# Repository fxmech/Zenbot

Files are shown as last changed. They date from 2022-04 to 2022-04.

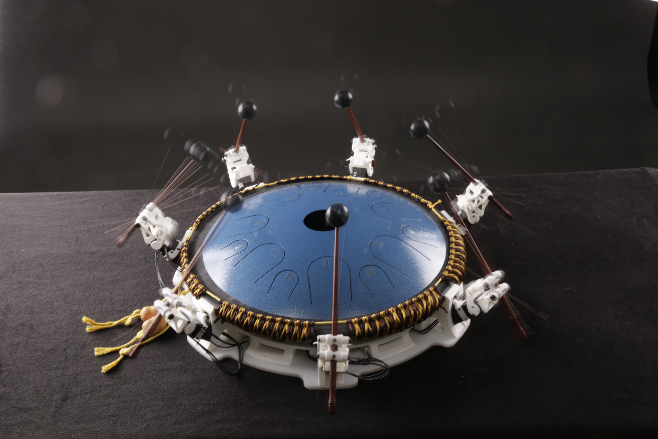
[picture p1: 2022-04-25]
_MG_4377.JPG

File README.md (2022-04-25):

# Zenbot
Zenbot is a project featured in MAKE Magazine that consists of seven robots playing 14 notes on a tongue drum
This repository will hold CAD files as well as arduino code.
Instructional videos to support the MAKE Magazine article can be found at:
https://www.youtube.com/playlist?list=PL2LZ_0VrozM2b-Bjvy_ZAQbU2o-aZzOwE
Article is available through https://makezine.com/

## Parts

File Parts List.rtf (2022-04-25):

Parts list:
ROBOTIS (https://www.robotis.us/ )
14 pcs Dynamixel xl330-m288-t servo
1 pk Robot cable X3P 240mm
2 pk Robot cable X3P 100mm
1 pk Robot cable X3P 180mm (Convertible)
1pc U2D2 (servo programmer)
1pc U2D2 Hub Board adapter
1pc OpenCM 485 Expansion Board
1pc OpenCM9.04-C microcontroller

Amazon
1pc AC to DC power adapter: AC Input: 100-240V 50/60Hz 1.0A, DC Output: 6V 3A
Amazon.com: Belker 36W Universal 3V 4.5V 5V 6V 7.5V 9V 12V AC DC Adapter Power Supply for LCD LED Light Strip Router HUB Speaker Smart Phone TV Box 1A 1.5A 2A 2.5A 3A 3000mA Amp Max. : Electronics (https://www.amazon.com/gp/product/B07N18XN84/ref=ppx_yo_dt_b_asin_title_o00_s00?ie=UTF8&psc=1)

1pk Generic 40 Pin Breakaway Headers 0.1" Male Equal Length Long Centered 6.25mm on Both Sides 15mm in Total(pack of 10)

5 Pcs 10k Linear Potentiometer, 10K Ohm 3 Pin Linear Taper Adjustable Rotary Potentiometer
https://www.amazon.com/Linear-Potentiometer-Adjustable-Connector-Resistance/dp/B09MS1T32Z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 (https://www.amazon.com/Linear-Potentiometer-Adjustable-Connector-Resistance/dp/B09MS1T32Z)

eBay
14inch Tongue Drum Handpan Pan Drum 14 Notes Hand Pan Drum Percussion Instrument
https://www.ebay.com/itm/233595745739

2pcs Wood Drum Sticks Steel Tongue Drum Mallets (4 come per order. You will need 7pcs total)
https://www.ebay.com/itm/184510420465

McMaster-Carr
10ft 3286T11 Buna-N O-Ring Cord, Oil-Resistant, 0.07" Actual Width, White
1 box 97763A143 Button Head 6-32 Thread Size, 1/2" Long screws (28 screws needed)
1 box 93791A453 Flat Head 6-32 Thread Size, 3/8" Long screws (21 screws needed)
97763A232 Button Head 10-32 Thread Size, 1/2" Long screws (28 screws needed)
92610A108 Socket Head 4-40 Thread Size, 1/4" Long screws (14 screws needed)
8505K757 Cast Acrylic Sheet, 24" x 24" x 1/4" Color: White

Optional:
4pks https://www.musiciansfriend.com/accessories/timber-drum-company-soft-rubber-mallets

Tools Used:
Computer and USB Micro Cable for programming Dynamixel servos (free online software needed)
3D printer with Tough PLA or other similar filament.
Hot Glue Gun
Drills, Taps, and reamers and countersink for finishing holes
Basic tools for cleaning 3d printed parts (sand paper, files, hobby knives, etc.)
Basic electronic tools (Iron, multimeter, wire, heat shrink, etc.)
Access to laser cutter or laser cutting service to cut base out of acrylic. Base can also be made from wood or 3d printed in smaller sections.

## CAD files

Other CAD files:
Zenbot.f3d

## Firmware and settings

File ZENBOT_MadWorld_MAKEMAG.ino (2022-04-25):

//ZENBOT 14-Servo Tongue Drum Player
//David Covarrubias
//fxmech@cammotion.net

#include <Dynamixel2Arduino.h>
#if defined(ARDUINO_AVR_UNO) || defined(ARDUINO_AVR_MEGA2560) // When using DynamixelShield
#include <SoftwareSerial.h>
SoftwareSerial soft_serial(7, 8); // DYNAMIXELShield UART RX/TX
#define DXL_SERIAL   Serial
#define DEBUG_SERIAL soft_serial
const uint8_t DXL_DIR_PIN = 2; // DYNAMIXEL Shield DIR PIN
#elif defined(ARDUINO_SAM_DUE) // When using DynamixelShield
#define DXL_SERIAL   Serial
#define DEBUG_SERIAL SerialUSB
const uint8_t DXL_DIR_PIN = 2; // DYNAMIXEL Shield DIR PIN
#elif defined(ARDUINO_SAM_ZERO) // When using DynamixelShield
#define DXL_SERIAL   Serial1
#define DEBUG_SERIAL SerialUSB
const uint8_t DXL_DIR_PIN = 2; // DYNAMIXEL Shield DIR PIN
#elif defined(ARDUINO_OpenCM904) // When using official ROBOTIS board with DXL circuit.
#define DXL_SERIAL   Serial3 //OpenCM9.04 EXP Board's DXL port Serial. (Serial1 for the DXL port on the OpenCM 9.04 board)
#define DEBUG_SERIAL Serial
const uint8_t DXL_DIR_PIN = 22; //OpenCM9.04 EXP Board's DIR PIN. (28 for the DXL port on the OpenCM 9.04 board)
#elif defined(ARDUINO_OpenCR) // When using official ROBOTIS board with DXL circuit.
#define DXL_SERIAL   Serial3
#define DEBUG_SERIAL Serial
const uint8_t DXL_DIR_PIN = 84; // OpenCR Board's DIR PIN.
#else // Other boards when using DynamixelShield
#define DXL_SERIAL   Serial1
#define DEBUG_SERIAL Serial
const uint8_t DXL_DIR_PIN = 2; // DYNAMIXEL Shield DIR PIN
#endif
const float DXL_PROTOCOL_VERSION = 2.0;

const int buttonPin = 16; //built in button on OpenCM Expansion Board
int buttonState = 0;

int malletRotateLowNote[8] = {0, 1975, 1975, 1975, 1975, 1975, 1975, 1997};//low octave
int malletRotateHighNote[8] = {0, 1776, 1776, 1795, 1730, 1753, 1800, 1731};//high octave
int malletUp = 1625;
int malletDown = 2121;

int reorder[8] = {0, 1, 3, 2, 7, 5, 4, 6}; 

int a;
int startFrame = 0;
int endFrame = 15;
int time2Move = 150; //millis that mallet spends dropping before it reverses direction

// 0= no note  1=low note loud  2= high note loud
int notesC[160] = {0, 0, 0, 0, 0, 0, 0, 0, 0, 0, 1, 0, 0, 0, 1, 0, 1, 0, 0, 0, 1, 0, 0, 0, 0, 0, 0, 0, 0, 0, 0, 0,    0, 0, 0, 0, 0, 0, 0, 0, 0, 0, 1, 0, 0, 0, 1, 0, 1, 0, 0, 0, 1, 0, 0, 0, 0, 0, 0, 0, 0, 0, 0, 0,   0, 0, 0, 0, 0, 0, 0, 0, 0, 0, 0, 0, 0, 0, 0, 0, 0, 0, 0, 0, 0, 0, 0, 0, 0, 0, 0, 0, 0, 0, 0, 0,    0, 0, 0, 0, 0, 0, 0, 0, 0, 0, 0, 0, 0, 0, 0, 0, 0, 0, 0, 0, 0, 0, 0, 0, 0, 0, 0, 0, 0, 0, 0, 0,    0, 0, 0, 0, 0, 0, 1, 0, 0, 0, 0, 0, 0, 0, 0, 0, 0, 0, 0, 0, 0, 0, 1, 0, 0, 0, 0, 0, 0, 0, 0, 0};
int notesD[160] = {1, 0, 1, 1, 0, 0, 2, 2, 0, 0, 0, 0, 0, 0, 0, 0, 0, 0, 0, 0, 0, 0, 0, 0, 0, 0, 1, 0, 0, 0, 1, 1,    0, 0, 1, 1, 0, 0, 2, 2, 0, 0, 0, 0, 0, 0, 0, 0, 0, 0, 0, 0, 0, 0, 0, 0, 1, 0, 0, 0, 0, 0, 0, 1,   0, 0, 1, 1, 1, 0, 0, 0, 0, 0, 1, 0, 0, 1, 1, 0, 1, 0, 0, 1, 1, 0, 0, 0, 0, 0, 1, 0, 0, 0, 1, 0,    2, 0, 1, 2, 1, 0, 0, 0, 0, 0, 1, 0, 0, 1, 1, 0, 1, 0, 0, 1, 1, 0, 0, 0, 1, 0, 0, 0, 0, 0, 0, 0,    1, 0, 0, 0, 1, 1, 0, 0, 0, 0, 1, 0, 0, 0, 1, 0, 1, 0, 0, 0, 1, 1, 0, 0, 0, 0, 1, 0, 0, 0, 1, 0};
int notesE[160] = {0, 0, 0, 0, 0, 0, 0, 0, 0, 0, 0, 0, 0, 0, 0, 0, 0, 0, 1, 0, 0, 1, 1, 0, 0, 0, 0, 0, 0, 0, 1, 0,    0, 0, 0, 0, 0, 0, 0, 0, 0, 0, 0, 0, 0, 0, 0, 0, 0, 0, 1, 0, 0, 1, 1, 0, 0, 0, 0, 0, 0, 0, 1, 0,   0, 0, 0, 0, 0, 0, 0, 0, 0, 0, 0, 0, 0, 0, 0, 0, 0, 0, 0, 0, 0, 0, 0, 0, 0, 0, 0, 0, 0, 0, 0, 0,    0, 0, 0, 0, 0, 0, 0, 0, 0, 0, 0, 0, 0, 0, 0, 0, 0, 0, 0, 0, 0, 0, 0, 0, 0, 0, 0, 0, 0, 0, 0, 0,    0, 0, 1, 1, 0, 0, 0, 0, 0, 0, 0, 0, 0, 0, 0, 0, 0, 0, 1, 1, 0, 0, 0, 0, 0, 0, 0, 0, 0, 0, 0, 0};
int notesF[160] = {0, 0, 1, 0, 2, 2, 1, 0, 1, 0, 0, 0, 1, 2, 0, 0, 0, 0, 0, 0, 0, 0, 0, 0, 0, 0, 0, 0, 0, 2, 0, 0,    0, 0, 1, 0, 2, 2, 1, 0, 1, 0, 0, 0, 1, 2, 0, 0, 0, 0, 0, 0, 0, 0, 0, 0, 0, 0, 0, 0, 0, 2, 0, 0,   0, 0, 1, 0, 2, 2, 1, 0, 0, 0, 0, 0, 0, 0, 0, 0, 0, 0, 1, 0, 2, 2, 2, 0, 0, 0, 0, 0, 0, 0, 0, 0,    0, 0, 0, 0, 2, 2, 1, 0, 0, 0, 0, 0, 0, 0, 0, 0, 0, 0, 1, 0, 2, 2, 2, 0, 0, 0, 0, 0, 0, 0, 0, 0,    2, 2, 1, 0, 2, 0, 1, 0, 0, 0, 0, 0, 0, 0, 0, 2, 0, 2, 1, 0, 2, 0, 1, 0, 0, 0, 0, 0, 0, 0, 0, 0};
int notesG[160] = {0, 0, 0, 0, 0, 0, 0, 0, 0, 0, 0, 0, 0, 0, 0, 0, 2, 2, 1, 2, 0, 0, 1, 0, 2, 2, 0, 2, 1, 0, 0, 0,    0, 0, 0, 0, 0, 0, 0, 0, 0, 0, 0, 0, 0, 0, 0, 0, 2, 2, 1, 2, 0, 0, 1, 0, 2, 2, 0, 2, 0, 0, 0, 0,   0, 0, 0, 0, 0, 0, 0, 0, 1, 2, 0, 2, 1, 0, 2, 2, 0, 0, 0, 0, 0, 0, 0, 0, 1, 2, 2, 2, 1, 0, 2, 2,    0, 0, 0, 0, 0, 0, 0, 0, 1, 2, 0, 2, 1, 0, 2, 2, 0, 0, 0, 0, 0, 0, 0, 0, 1, 2, 2, 2, 0, 0, 2, 2,    0, 0, 0, 0, 0, 0, 0, 0, 1, 0, 0, 0, 1, 0, 0, 0, 0, 0, 0, 0, 0, 0, 0, 2, 1, 0, 0, 0, 1, 0, 0, 0};
int notesA[160] = {0, 0, 1, 0, 0, 0, 1, 0, 2, 2, 1, 2, 0, 0, 1, 0, 0, 0, 0, 0, 0, 0, 0, 0, 0, 0, 0, 0, 0, 0, 0, 0,    0, 0, 1, 0, 0, 0, 1, 0, 2, 2, 1, 2, 0, 0, 1, 0, 0, 0, 0, 0, 0, 0, 0, 0, 0, 0, 0, 0, 0, 0, 0, 0,   0, 0, 1, 0, 0, 0, 2, 2, 0, 0, 0, 0, 0, 0, 0, 0, 0, 0, 1, 0, 0, 0, 2, 2, 0, 0, 1, 0, 0, 0, 1, 0,    0, 0, 1, 0, 0, 0, 2, 2, 0, 0, 0, 0, 0, 0, 0, 0, 0, 0, 1, 0, 0, 0, 2, 2, 0, 0, 0, 0, 0, 0, 0, 0,    2, 2, 1, 0, 0, 0, 1, 0, 0, 0, 0, 0, 0, 0, 0, 0, 0, 2, 1, 0, 0, 0, 1, 0, 0, 0, 0, 0, 0, 0, 0, 0};
int notesB[160] = {0, 0, 0, 0, 0, 0, 0, 0, 0, 0, 0, 0, 0, 0, 0, 0, 0, 0, 0, 0, 0, 0, 0, 0, 0, 0, 1, 0, 0, 0, 1, 0,    0, 0, 0, 0, 0, 0, 0, 0, 0, 0, 0, 0, 0, 0, 0, 0, 0, 0, 0, 0, 0, 0, 0, 0, 1, 0, 0, 0, 0, 0, 0, 0,   0, 0, 0, 0, 0, 0, 0, 0, 2, 0, 1, 0, 2, 2, 1, 0, 0, 0, 0, 0, 0, 0, 0, 0, 2, 0, 0, 0, 2, 2, 0, 0,    0, 0, 0, 0, 0, 0, 0, 0, 2, 0, 1, 0, 2, 2, 1, 0, 0, 0, 0, 0, 0, 0, 0, 0, 2, 0, 0, 0, 2, 2, 0, 0,    0, 0, 0, 0, 0, 0, 0, 1, 0, 0, 1, 0, 0, 0, 1, 0, 0, 0, 0, 0, 0, 0, 0, 1, 0, 0, 1, 0, 0, 0, 1, 0};

Dynamixel2Arduino dxl(DXL_SERIAL, DXL_DIR_PIN);

//This namespace is required to use Control table item names
using namespace ControlTableItem;

void setup() {
  pinMode(buttonPin, INPUT); //Start Button Pin

  // Use UART port of DYNAMIXEL Shield to debug.
  //DEBUG_SERIAL.begin(115200);
  //while(!DEBUG_SERIAL);
  dxl.begin(1000000);
  // Set Port Protocol Version. This has to match with DYNAMIXEL protocol version.
  dxl.setPortProtocolVersion(DXL_PROTOCOL_VERSION);
  // Get DYNAMIXEL information
  for (int i = 1; i < 8; i++) {
    dxl.ping(i);
    dxl.ping(i + 10);
    delay(100);
  }

  // Turn off torque when configuring items in EEPROM area
  for (int i = 1; i < 8; i++) {
    dxl.torqueOff(i);
    dxl.setOperatingMode(i, OP_POSITION);
    dxl.torqueOn(i);
    dxl.torqueOff(i + 10);
    dxl.setOperatingMode(i + 10, OP_POSITION);
    dxl.torqueOn(i + 10);
    delay(100);
  }

  // Limit the maximum velocity in Position Control Mode. Use 0 for Max speed
  for (int i = 1; i < 8; i++) {
    dxl.writeControlTableItem(PROFILE_VELOCITY, i, 0);
    dxl.writeControlTableItem(PROFILE_VELOCITY, i + 10, 0);
    dxl.writeControlTableItem(PROFILE_ACCELERATION, i, 0);
    dxl.writeControlTableItem(PROFILE_ACCELERATION, i + 10, 0);
    dxl.setGoalPosition(i, 2024);
    dxl.setGoalPosition(i + 10, 1750);
    delay(100);
  }
  delay(500);
  startAnimation();
}
void playnotesA(int del) {
  startFrame = 0;
  endFrame = 31;

  for (int i = startFrame; i < endFrame + 1; i++) {
    // STRIKE NOTE
    if (notesC[i] == 1 || notesC[i] == 2)  dxl.setGoalPosition(11, malletDown);
    if (notesD[i] == 1 || notesD[i] == 2)  dxl.setGoalPosition(12, malletDown);
    if (notesE[i] == 1 || notesE[i] == 2)  dxl.setGoalPosition(13, malletDown);
    if (notesF[i] == 1 || notesF[i] == 2)  dxl.setGoalPosition(14, malletDown);
    if (notesG[i] == 1 || notesG[i] == 2)  dxl.setGoalPosition(15, malletDown);
    if (notesA[i] == 1 || notesA[i] == 2)  dxl.setGoalPosition(16, malletDown);
    if (notesB[i] == 1 || notesB[i] == 2)  dxl.setGoalPosition(17, malletDown);
    delay(time2Move);

    //PREP FOR NEXT NOTE
    if (i + 1 >= endFrame + 1) a = startFrame; else a = i + 1;
    if (notesC[a] == 1)dxl.setGoalPosition(1, malletRotateLowNote[1]); else dxl.setGoalPosition(1, malletRotateHighNote[1]);
    if (notesD[a] == 1)dxl.setGoalPosition(2, malletRotateLowNote[2]); else dxl.setGoalPosition(2, malletRotateHighNote[2]);
    if (notesE[a] == 1)dxl.setGoalPosition(3, malletRotateLowNote[3]); else dxl.setGoalPosition(3, malletRotateHighNote[3]);
    if (notesF[a] == 1)dxl.setGoalPosition(4, malletRotateLowNote[4]); else dxl.setGoalPosition(4, malletRotateHighNote[4]);
    if (notesG[a] == 1)dxl.setGoalPosition(5, malletRotateLowNote[5]); else dxl.setGoalPosition(5, malletRotateHighNote[5]);
    if (notesA[a] == 1)dxl.setGoalPosition(6, malletRotateLowNote[6]); else dxl.setGoalPosition(6, malletRotateHighNote[6]);
    if (notesB[a] < 3)dxl.setGoalPosition(7, malletRotateLowNote[7]); else dxl.setGoalPosition(7, malletRotateHighNote[7]);
    for (int i = 11; i < 18; i++) {
      dxl.setGoalPosition(i, malletUp);
    }
    delay(del);
  }
}

void playnotesB(int del) {
  startFrame = 32;
  endFrame = 63;

  for (int i = startFrame; i < endFrame + 1; i++) {
    // STRIKE NOTE
    if (notesC[i] == 1 || notesC[i] == 2)  dxl.setGoalPosition(11, malletDown);
    if (notesD[i] == 1 || notesD[i] == 2)  dxl.setGoalPosition(12, malletDown);
    if (notesE[i] == 1 || notesE[i] == 2)  dxl.setGoalPosition(13, malletDown);
    if (notesF[i] == 1 || notesF[i] == 2)  dxl.setGoalPosition(14, malletDown);
    if (notesG[i] == 1 || notesG[i] == 2)  dxl.setGoalPosition(15, malletDown);
    if (notesA[i] == 1 || notesA[i] == 2)  dxl.setGoalPosition(16, malletDown);
    if (notesB[i] == 1 || notesB[i] == 2)  dxl.setGoalPosition(17, malletDown);
    delay(time2Move);

    //PREP FOR NEXT NOTE
    if (i + 1 >= endFrame + 1) a = startFrame; else a = i + 1;
    if (notesC[a] == 1)dxl.setGoalPosition(1, malletRotateLowNote[1]); else dxl.setGoalPosition(1, malletRotateHighNote[1]);
    if (notesD[a] == 1)dxl.setGoalPosition(2, malletRotateLowNote[2]); else dxl.setGoalPosition(2, malletRotateHighNote[2]);
    if (notesE[a] == 1)dxl.setGoalPosition(3, malletRotateLowNote[3]); else dxl.setGoalPosition(3, malletRotateHighNote[3]);
    if (notesF[a] == 1)dxl.setGoalPosition(4, malletRotateLowNote[4]); else dxl.setGoalPosition(4, malletRotateHighNote[4]);
    if (notesG[a] == 1)dxl.setGoalPosition(5, malletRotateLowNote[5]); else dxl.setGoalPosition(5, malletRotateHighNote[5]);
    if (notesA[a] == 1)dxl.setGoalPosition(6, malletRotateLowNote[6]); else dxl.setGoalPosition(6, malletRotateHighNote[6]);
    if (notesB[a] == 1)dxl.setGoalPosition(7, malletRotateLowNote[7]); else dxl.setGoalPosition(7, malletRotateHighNote[7]);
    for (int i = 11; i < 18; i++) {
      dxl.setGoalPosition(i, malletUp);
    }
    delay(del);
  }
}

void playnotesC(int del) {
  startFrame = 64;
  endFrame = 160;

  for (int i = startFrame; i < endFrame + 1; i++) {
    // STRIKE NOTE
    if (notesC[i] == 1 || notesC[i] == 2)  dxl.setGoalPosition(11, malletDown);
    if (notesD[i] == 1 || notesD[i] == 2)  dxl.setGoalPosition(12, malletDown);
    if (notesE[i] == 1 || notesE[i] == 2)  dxl.setGoalPosition(13, malletDown);
    if (notesF[i] == 1 || notesF[i] == 2)  dxl.setGoalPosition(14, malletDown);
    if (notesG[i] == 1 || notesG[i] == 2)  dxl.setGoalPosition(15, malletDown);
    if (notesA[i] == 1 || notesA[i] == 2)  dxl.setGoalPosition(16, malletDown);
    if (notesB[i] == 1 || notesB[i] == 2)  dxl.setGoalPosition(17, malletDown);
    delay(time2Move);

    //PREP FOR NEXT NOTE
    if (i + 1 >= endFrame + 1) a = startFrame; else a = i + 1;
    if (notesC[a] == 1)dxl.setGoalPosition(1, malletRotateLowNote[1]); else dxl.setGoalPosition(1, malletRotateHighNote[1]);
    if (notesD[a] == 1)dxl.setGoalPosition(2, malletRotateLowNote[2]); else dxl.setGoalPosition(2, malletRotateHighNote[2]);
    if (notesE[a] == 1)dxl.setGoalPosition(3, malletRotateLowNote[3]); else dxl.setGoalPosition(3, malletRotateHighNote[3]);
    if (notesF[a] == 1)dxl.setGoalPosition(4, malletRotateLowNote[4]); else dxl.setGoalPosition(4, malletRotateHighNote[4]);
    if (notesG[a] == 1)dxl.setGoalPosition(5, malletRotateLowNote[5]); else dxl.setGoalPosition(5, malletRotateHighNote[5]);
    if (notesA[a] == 1)dxl.setGoalPosition(6, malletRotateLowNote[6]); else dxl.setGoalPosition(6, malletRotateHighNote[6]);
    if (notesB[a] == 1)dxl.setGoalPosition(7, malletRotateLowNote[7]); else dxl.setGoalPosition(7, malletRotateHighNote[7]);
    for (int i = 11; i < 18; i++) {
      dxl.setGoalPosition(i, malletUp);
    }
    delay(del);
  }
}
void lowerAllMallets() { //Slowly lowers all mallets to surface of drum
  for (int i = 1; i < 8; i++) {
    dxl.writeControlTableItem(PROFILE_VELOCITY, i + 10, 30);
    dxl.setGoalPosition(i + 10, malletDown);
    delay(10);
  }
  delay(1000);

  for (int i = 1; i < 8; i++) {
    dxl.writeControlTableItem(PROFILE_VELOCITY, i + 10, 0);
    delay(10);
  }
}
void prepFirstNotes() {
  for (int i = 11; i < 18; i++) { //Mallets UP
    dxl.setGoalPosition(i, malletUp);
    delay(100);
  }
  //PREP FOR FIRST NOTE
  a = 0;
  if (notesC[a] == 1)dxl.setGoalPosition(1, malletRotateLowNote[1]); else dxl.setGoalPosition(1, malletRotateHighNote[1]);
  if (notesD[a] == 1)dxl.setGoalPosition(2, malletRotateLowNote[2]); else dxl.setGoalPosition(2, malletRotateHighNote[2]);
  if (notesE[a] == 1)dxl.setGoalPosition(3, malletRotateLowNote[3]); else dxl.setGoalPosition(3, malletRotateHighNote[3]);
  if (notesF[a] == 1)dxl.setGoalPosition(4, malletRotateLowNote[4]); else dxl.setGoalPosition(4, malletRotateHighNote[4]);
  if (notesG[a] == 1)dxl.setGoalPosition(5, malletRotateLowNote[5]); else dxl.setGoalPosition(5, malletRotateHighNote[5]);
  if (notesA[a] == 1)dxl.setGoalPosition(6, malletRotateLowNote[6]); else dxl.setGoalPosition(6, malletRotateHighNote[6]);
  if (notesB[a] == 1)dxl.setGoalPosition(7, malletRotateLowNote[7]); else dxl.setGoalPosition(7, malletRotateHighNote[7]);
  delay(500);
}

void torqueAllOn() { //turns all servos on
  for (int i = 1; i < 8; i++) {
    dxl.torqueOn(i);
    dxl.torqueOn(i + 10);
    delay(100);
  }
  delay(500);
}

void torqueAllOff() { //turns all servos off
  for (int i = 1; i < 8; i++) {
    dxl.torqueOff(i);
    dxl.torqueOff(i + 10);
    delay(100);
  }
  delay(500);
}

void startAnimation() {
  //All Mallets up and Center
  for (int i = 1; i < 8; i++) {
    dxl.setGoalPosition(i, 2024);
    dxl.setGoalPosition(i + 10, 1712);
  }
  delay(400);
  //All Mallets rotate side one at a time
  for (int i = 1; i < 8; i++) {
    dxl.setGoalPosition(reorder[i], 1730);
    delay(100);
  }
  delay(400);
  //All Mallets rotate center one at a time
  for (int i = 1; i < 8; i++) {
    dxl.setGoalPosition(reorder[i], 2024);
    delay(100);
  }
  delay(400);
  //All Mallets rotate side at once
  for (int i = 1; i < 8; i++) {
    dxl.setGoalPosition(reorder[i], 1730);
  }
  delay(700);
  //All Mallets rotate to start position
  for (int i = 1; i < 8; i++) {
    dxl.setGoalPosition(i, malletRotateLowNote[i]);
    dxl.setGoalPosition(i, 1712);
  }
  delay(700);

  //All Mallets rotate side at once
  for (int i = 1; i < 8; i++) {
    dxl.setGoalPosition(reorder[i], 1730);
  }
  delay(150);
  //All Mallets rotate to start position
  for (int i = 1; i < 8; i++) {
    dxl.setGoalPosition(i, malletRotateLowNote[i]);
    dxl.setGoalPosition(i, 1712);
  }
  delay(150);
  //All Mallets rotate side at once
  for (int i = 1; i < 8; i++) {
    dxl.setGoalPosition(reorder[i], 1730);
  }
  delay(150);
  //All Mallets rotate to start position
  for (int i = 1; i < 8; i++) {
    dxl.setGoalPosition(i, malletRotateLowNote[i]);
    dxl.setGoalPosition(i, 1712);
  }
  delay(1000);
  lowerAllMallets();//go to neutral Position and lower mallets slowly
  torqueAllOff();//Torques Servos Off
}

void loop() {
  buttonState = digitalRead(buttonPin); // check for button press
  if (buttonState == HIGH) { //if button is pressed then play song
    torqueAllOn(); //Torques Servos On
    prepFirstNotes();//Move to first note Start Position
    playnotesA(100); //plays sequence A at tempo of Millis between notes
    playnotesB(100);
    playnotesC(100);
    lowerAllMallets();//go to neutral Position and lower mallets slowly
    torqueAllOff();//Torques Servos Off
  }
}

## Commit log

2022-04-25 Add files via upload
    Arduino files must be stored in a like named folder.
2022-04-25 Add files via upload
    CAD Files for Zenbot Build
    [Zenbot.f3d]
